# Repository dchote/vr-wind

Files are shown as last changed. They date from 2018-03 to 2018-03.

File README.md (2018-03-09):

# vr-wind
Arduino based DIY Wind implementation for Assetto Corsa &amp; other games.

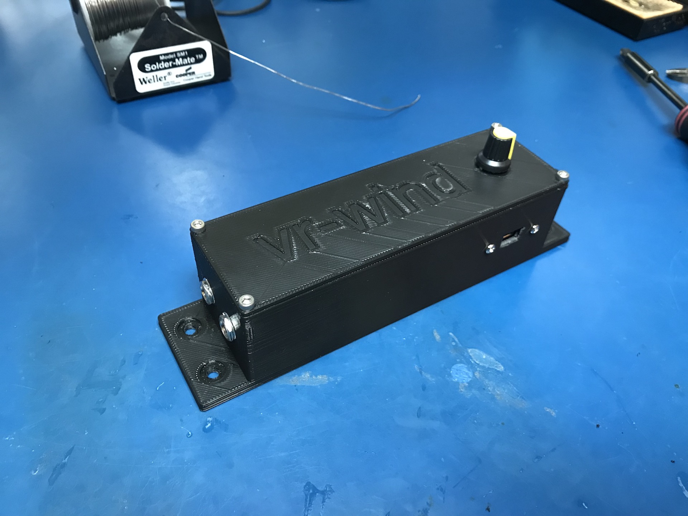
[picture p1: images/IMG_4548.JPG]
assembled1 Assembled wind-vr controller

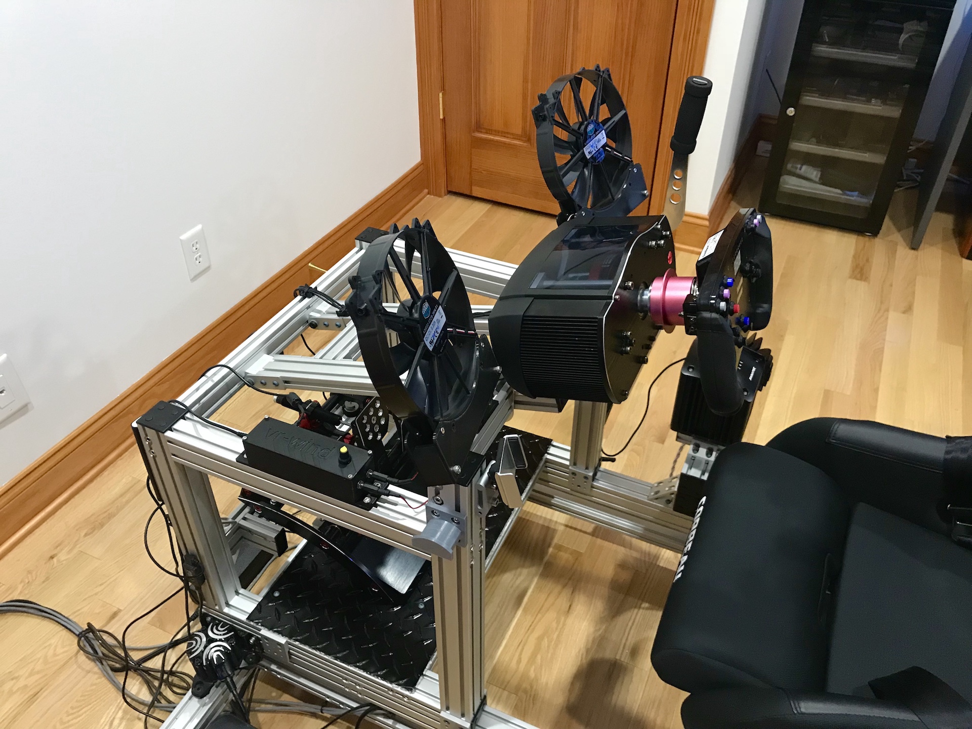
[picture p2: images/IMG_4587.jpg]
assembled3 Assembled wind-vr on my motion rig


## 3D printable parts
In the [stl](stl/) directory are the stl files for the enclosure and the fan mounts. 
You should may need a large format 3D printer to print some of these parts.

## Arduino controller

The Arduino code [here](arduino/vr-wind/) is designed to work on an Arduino Pro Micro 5v, 
using pins 9 &amp; 10 for PWM output through some sort of darlington transistor solution. 

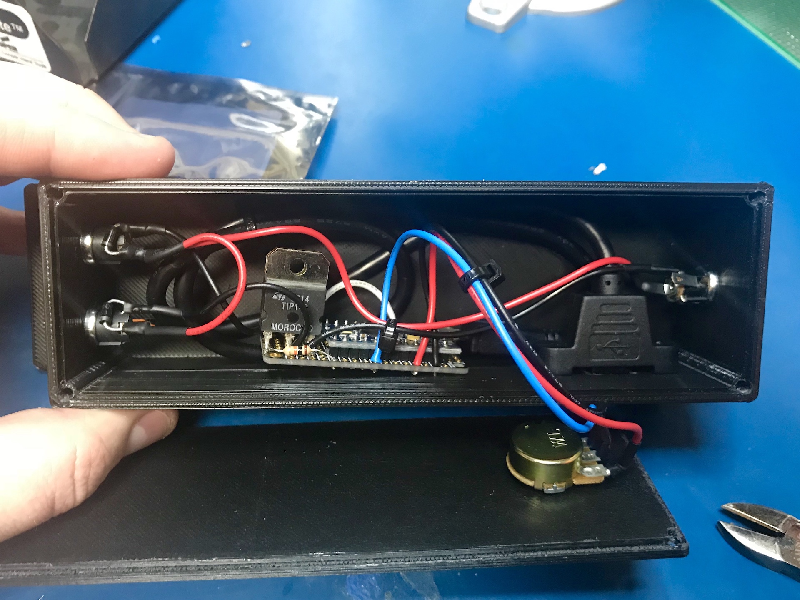
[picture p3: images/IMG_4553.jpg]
assembled2 Assembled wind-vr controller


I used a pair of TIP142s that I already had. The wiring is very simple. Use a 1k (or so) current limiting resistor to the transistor base, 
shared ground (negative) on the emitter, arduino ground, and to your 12v or 24v supply. The collector of the transistor goes to the negative input of your motor. 
Positive on the motor goes directly to the positive supply.
You MUST include a diode across your motor to deal with the backflow from the coil. 

You can read more about this configuration [here](http://www.instructables.com/id/Use-Arduino-with-TIP120-transistor-to-control-moto/).

## Game plugins

* [Assetto Corsa](plugins/Assetto%20Corsa)

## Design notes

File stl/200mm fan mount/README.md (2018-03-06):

This mount is for the CoolerMaster MegaFlow 200 Silent Fan: http://www.coolermaster.com/cooling/case-fan/megaflow-200-silent-fan/

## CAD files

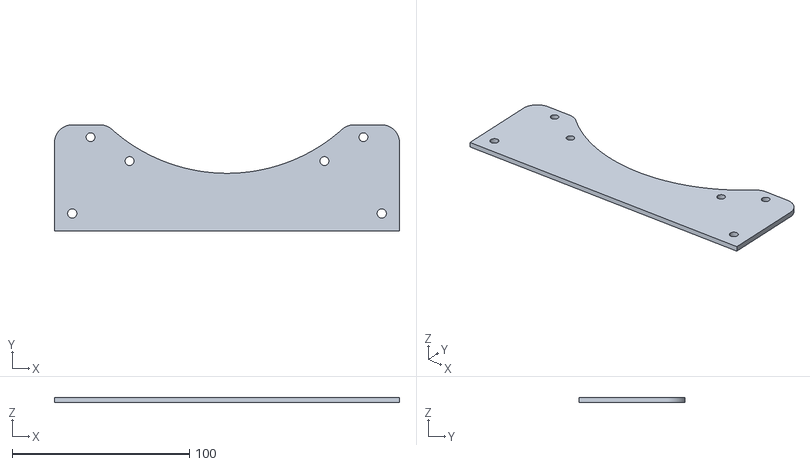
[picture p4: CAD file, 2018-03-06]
stl/200mm fan mount/Side Panel.stl
194.7 x 60.0 x 3.00

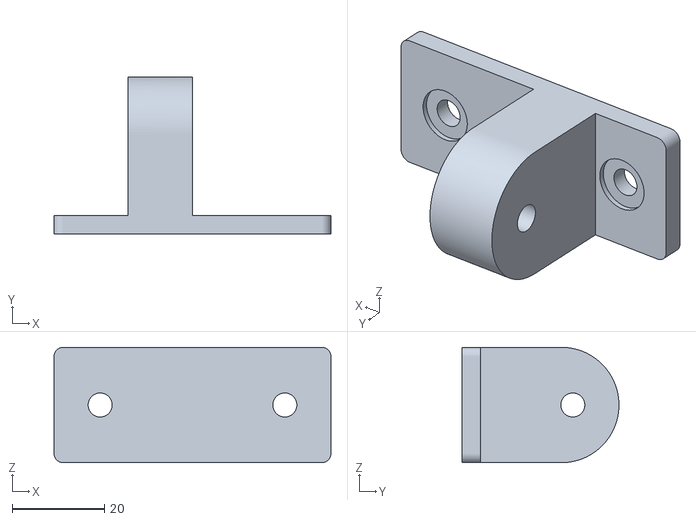
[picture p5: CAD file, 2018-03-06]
stl/8020 Mount.stl
60.0 x 34.0 x 25.0

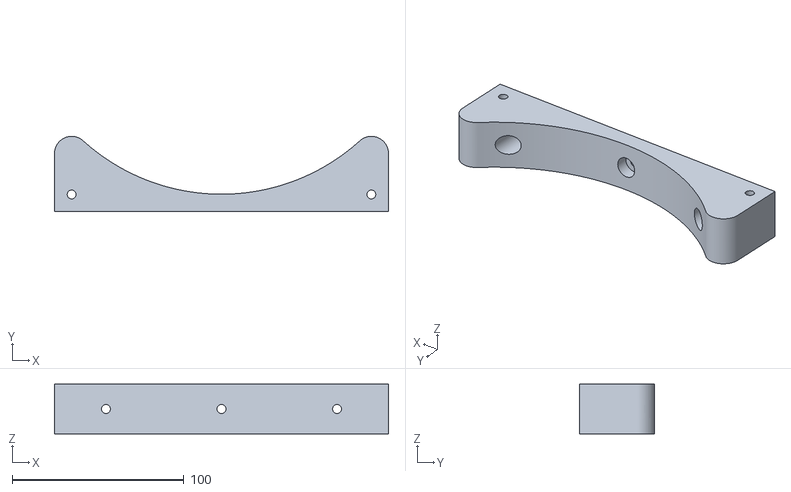
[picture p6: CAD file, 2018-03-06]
stl/200mm fan mount/Body.stl
194.7 x 43.9 x 29.0

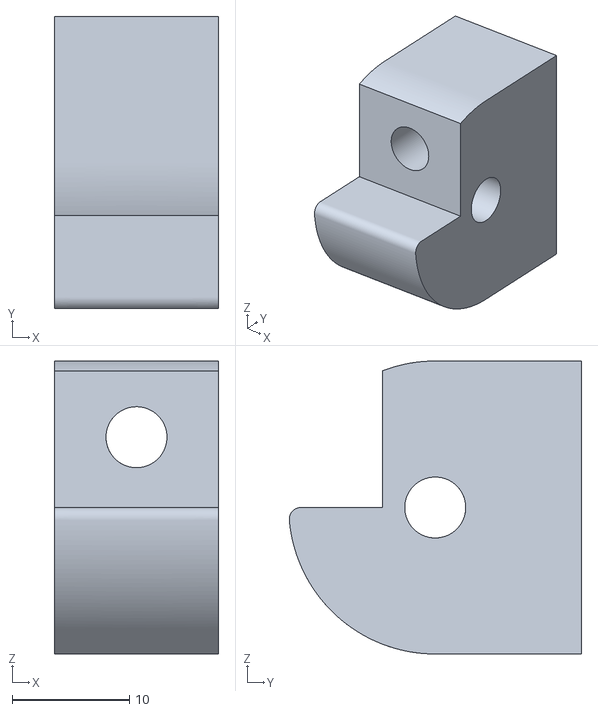
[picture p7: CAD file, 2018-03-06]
stl/Swivel Bracket.stl
14.0 x 25.0 x 25.0

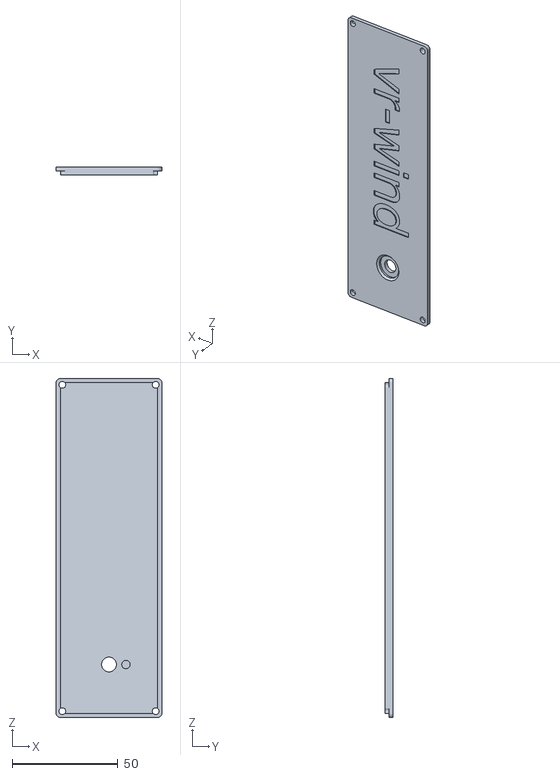
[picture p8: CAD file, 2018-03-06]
stl/Controller Lid.stl
50.0 x 4.00 x 160.0

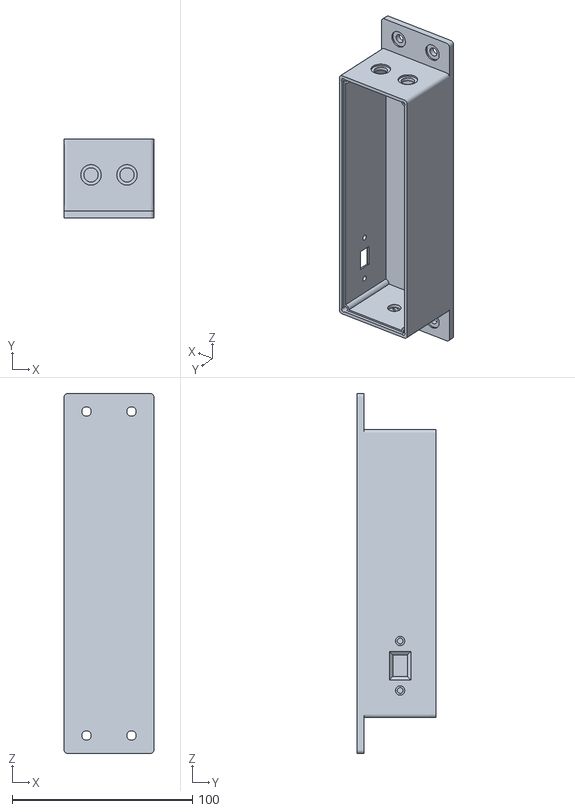
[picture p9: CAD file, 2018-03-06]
stl/Controller Box.stl
50.0 x 44.0 x 200.0

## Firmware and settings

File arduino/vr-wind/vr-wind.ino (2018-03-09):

/*
  vr-wind
  By Daniel Chote 2018
  https://github.com/dchote/vr-wind
*/

#include <elapsedMillis.h>

// Pins
int leftFanPin = 9;
int rightFanPin = 10;

int fanAdjustPin = 0;

// state
elapsedMillis timeElapsed;
int fanValueTimeout = 3000; // 3 second timeout

int fanAdjustValue = 0;

int minFanSpeed = 0;
int maxFanSpeed = 0;

int leftFanValue = 0;
int rightFanValue = 0;

int leftFanSpeed = 0;
int rightFanSpeed = 0;

void setup() {
  Serial.begin(9600);
  Serial.println();
  
  delay(500);
  
  Serial.println("vr-wind");
  timeElapsed = 0;
  
  pinMode(leftFanPin, OUTPUT);
  pinMode(rightFanPin, OUTPUT);
  
  // set PWM mode
  TCCR1B = (TCCR1B & 0b11111000) | 0x01;
}

void loop() {
  fanAdjustValue = map(analogRead(fanAdjustPin), 0, 1023, 0, 255);
  
  if (fanAdjustValue < 10) {
    // turn off fans
    minFanSpeed = 0;
    maxFanSpeed = 0;
  } else {
    if (fanAdjustValue < 250) {
      // allow fan to not spin if not needed
      minFanSpeed = 0;
    } else {
      // low fan idle speed
      minFanSpeed = 15;
    }
    
    maxFanSpeed = 255;
  }
  
  int serialTimeout = 0;
  while (Serial.available() > 0) {
    serialTimeout++;
    
    leftFanValue = Serial.parseInt();
    Serial.read(); // seperator
    rightFanValue = Serial.parseInt();
    
    if (Serial.read() == '\n') {
      timeElapsed = 0;
      /*
      Serial.print("Recieved: ");
      Serial.print(leftFanValue);
      Serial.print(" ");
      Serial.print(rightFanValue);
      Serial.print(" Min: ");
      Serial.print(minFanSpeed);
      Serial.print(" Max: ");
      Serial.print(maxFanSpeed);
      Serial.println();
      */
      break;
    }
    
    if (serialTimeout > 100) break;
  }
  
  
  if ((leftFanValue > 0 || rightFanValue > 0) && timeElapsed > fanValueTimeout) {
    //Serial.println("timeout");
    leftFanValue = minFanSpeed;
    rightFanValue = minFanSpeed;
    timeElapsed = 0;
  }
  
  // lets scale fan speed in to buckets, this is arbitrary based off what I felt seemed right.
  leftFanSpeed = fanSpeedAdjust(calculateFanSpeed(leftFanValue));
  rightFanSpeed = fanSpeedAdjust(calculateFanSpeed(rightFanValue));
  
  analogWrite(leftFanPin, leftFanSpeed);
  analogWrite(rightFanPin, rightFanSpeed);
  
  // debug print current values
  /*
  Serial.print("Left Speed: ");
  Serial.print(leftFanSpeed);
  Serial.print(" Right Speed: ");
  Serial.print(rightFanSpeed);
  Serial.println();
  
  delay(500);
  */
}

int calculateFanSpeed(int requestedValue) 
{
  if (requestedValue == 0) {
    return 0;
  } else if (requestedValue <= 50) {
    return map(requestedValue, 0, 50, 10, 18);
  } else if (requestedValue <= 100) {
    return map(requestedValue, 50, 100, 18, 25);
  } else if (requestedValue <= 150) {
    return map(requestedValue, 100, 150, 25, 50);
  } else {
    return map(requestedValue, 150, 255, 50, 255);
  }
}

int fanSpeedAdjust(int requestedSpeed)
{
  float adjustment = (float)fanAdjustValue / 255;
  
  requestedSpeed = round((float)requestedSpeed * adjustment);
  
  if (requestedSpeed < minFanSpeed) {
    requestedSpeed = minFanSpeed;
  }
  
  if (requestedSpeed > maxFanSpeed) {
    requestedSpeed = maxFanSpeed;
  }
  
  return requestedSpeed;
}

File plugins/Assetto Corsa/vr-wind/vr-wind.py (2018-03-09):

#
#  vr-wind
#  By Daniel Chote 2018
#  https://github.com/dchote/vr-wind
#

import sys
import os
import platform
import time

if platform.architecture()[0] == "64bit":
    sysdir = "stdlib64"
else:
    sysdir = "stdlib"

sys.path.insert(0, os.path.join(os.path.dirname(__file__), sysdir))
os.environ['PATH'] = os.environ['PATH'] + ";."

import ac

ac.log("python platform.architecture=" + str(platform.architecture()) + "; sys.version=" + str(sys.version))

import acsys
import serial

ac.log("modules imported")

# EDIT THIS
# update serialPortName to reflect the COM port on your system
serialPortName = 'COM9'


# DO NOT EDIT PAST THIS POINT
appWindow = 0
statusLabel = 0

serPort = 0
tick = 0


def acMain(acVerison):
    global serPort, tick, appWindow, statusLabel
    
    try:
        ac.log("opening serial port {}".format(serialPortName))
        
        tick = ticker() # class below: keeps track of game tick rate and can be used to update over serial less frequently
        
        serPort = serial.Serial(port = serialPortName, baudrate = 9600, timeout = 0)
        time.sleep(3)
        serPort.write("0 0 \n".encode())
        
        appWindow = ac.newApp("vr-wind")
        ac.setSize(appWindow, 200, 200)
        
        statusLabel = ac.addLabel(appWindow, "Output: none yet");
        ac.setPosition(statusLabel, 5, 32)
        
        ac.log("vr-wind ready")
        
        return "vr-wind"
        
    except Exception as e:
        ac.log("startup error: {}".format(e))
 

def acUpdate(deltaT):  
    global serPort, tick, appWindow, statusLabel
    
    if tick.tack(deltaT):
        return
    
    try:        
        speed = str(round(ac.getCarState(0, acsys.CS.SpeedMPH)))
        # TODO implement acsys.CS.Steer to adjust left vs right speeds
        
        # speed in MPH, we handle the speed states on the controller
        command = speed + " " + speed + "\n"
        serPort.write(command.encode())
        
        ac.setText(statusLabel, "Output: {}".format(command))
        
    except Exception as e:
        ac.log("update error: {}".format(e))


def acShutdown(deltaT):  
    global serPort, tick, appWindow, statusLabel
    
    ac.log("shutdown called")
    ac.setText(statusLabel, "Shutting down")
    
    command = "0 0\n"
    serPort.write(command.encode())
    
    if (serPort == 0): return
    
    try:
        serPort.close()

    except Exception as e:
        ac.log("shutdown error: {}".format(e))
        
        
        
#-----------------------
# ticker function, to determine update rate
#--------------------
class ticker:
    def __init__(self):
        self.ticktimer = 0.0
        self.ticktime = 0.0
        self.tickrate = 0.5 # update rate in seconds
   
    def tack(self,deltaT):
        self.ticktime += deltaT
        self.ticktimer += deltaT
        if self.ticktime >= self.tickrate:
            self.ticktime = self.ticktime % self.tickrate
            return False
        else:
            return True
   
    def debuginfo(self):
        return "ticktimer: %s ticktime: %s tickrate: %s" % (self.ticktimer, self.ticktime, self.tickrate)

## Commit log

2018-03-06 Initial stl import Initial test code for Arduino
    [8020 Mount.stl, Body.stl, Controller Box.stl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]
2018-03-06 Functional code pushed serial protocol is just 2 integers (PWM value) and a newline. example: "128 128\n"
2018-03-07 Update Arduino code for use on Leonardo Initial commit of untested Assetto Corsa plugin
2018-03-07 Assetto Corsa app fixes Assetto Corsa app window with basic output information Arduino code tuning Arduino code timeout that resets the fans after 3 seconds without an update
    [vr-wind.ino, vr-wind.py]
2018-03-09 Changed the expected protocol to MPH vs PWM to allow better granularity of fan speeds Added a new mechanism to scale fan speed Changed the function of the potentiometer to correctly scale the speed r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
    [vr-wind.ino, vr-wind.py]
